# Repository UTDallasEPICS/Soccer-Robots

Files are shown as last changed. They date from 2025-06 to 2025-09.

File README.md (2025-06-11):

# Soccer Robots CS (UTDesign EPICS)

<!-- markdownlint-disable-next-line MD033 -->
<details><summary><h2>Table of Contents</h2></summary>

- [Conceptual Overview](#conceptual-overview)
- [Repository Branches Map](#repository-branches-map)
- [Functional Requirements](#functional-requirements)
- [Third Party Integrations](#third-party-integrations)
- [Tech Stack](#tech-stack)
- [Deployment Notes](#deployment-notes)
- [Migration Scripts](#migration-scripts)
- [Setting Up Development Environment](#setting-up-development-environment)

</details>

## Conceptual Overview

The Jonsson School UTDesign program serves students from UTDesign Capstone, EPICS, Makerspace and Startup. Our partner is Tim Givens, the UTDesign Studio Assistant Manager, who has the following mission:

*To bring UTD to the forefront of robotics competitions while collaborating with local high schools to get more kids engaged in robotics and STEM.*

Soccer Robots is an interactive live-fed soccer game between two robots where players can control their robots remotely over the internet. The Soccer Robots team is split into CS and Engineering teams. We are Soccer Robots CS, tasked with

- Handle serving webpage
- Handle user accounts through Auth0
- Integrate Twitch livestream
- Display game information such as time and scoreboard
- Implement queue system
- Set up and record matches
- Forward wasd inputs from players to Engineering team (Raspberry server)
- Communicate with Engineering team for robots' status

Our project not only caters to the entertainment needs of our users but also serves as a captivating demonstration of UTDesign's capabilities!

## Repository Branches Map
- main: Website / user side of project
- main_robot: Main branch for the robot side of the project
  - esp32_code: Development branch for robot side of the project
- raspberry_pi: Main branch for web/game server code. A raspberry pi is used to host the website, manage the game, and bridge control from user to robots.
  - oled_pi: Contains a service script that runs on raspberry pi startup. This displays IP information of the raspberry pi. 

## Users/Roles

#### Guest

- can watch the game

#### Registered User

- can watch the game
- join/leave/confirm queue
- can play the game (wasd inputs)

#### Admin 

- The Admin shall be able to change match settings
- The Admin shall be able shutdown the Robot

## Functional Requirements

### Website

- The website shall display a game livestream in under 10 second latency
- The website shall display a timer/scoreboard for the current match, showing the usernames of the players as well as their respective scores
- The website shall display the game queue
- The website shall display additional information such as About Us, How to Play, and Help
- The user shall be able to login and logout through Auth0
- The user shall be able to select a new username
- Newly registered users shall be able choose a unique username (2-15 characters, alphanumeric except for dashes ```-``` and underscores ```_```)

### Queue System

- Logged in users shall be able to click on a “Join Queue” button to enter the queue
- Users in the queue shall be able to click on a “Leave Queue” button to leave the queue
- The queue shall not allow duplicate users in the queue
- The queue shall display multiple upcoming matches by placing later matches below earlier matches
- When a match is done and there are at least two players in the queue, the system shall send a confirmation popup to the next two players in the queue with the option to “Accept” or “Decline”
  - In a confirmation popup, the player shall be able to click “Accept” within 10 seconds to agree to join the match
  - When both players of a confirmation popup click “Accept”, both players shall be able to enter a soccer robot match and each control a robot
  - In a confirmation popup, the player shall be able to click “Decline” within 10 seconds to refuse to join the match and leave the queue
  - In a confirmation popup, the system shall kick a player from the queue if the player does not click either “Accept” or “Decline” within 10 seconds

### Admin Panel

- User with an admin privileges can shutdown the robot.
- User with admin privileges can also change the match settings such as match length, num of players in a match.
- The Admin panel will be pn the secondary navbar adn when clicked we will get a popuo
  - The popup has two buttons that says shutdown and match settings
    - When users clicks on shutdown it verifies the user previleges and if admin it sends signal to the raspberry pi.
    - when clicked on match settings we wll get a drop down that asks for number of players and match length. The data is saved in the database when clicked save.

### Leaderboard

- The leaderboard shall show the columns of the players wins, losses, total goals scored, total games played, and win/loss ratio
- The leaderboard should appear in modal
- The leaderboard shall be shortable by the columns representing: goals, wins, losses, win/loss ratio, and games played of each player
- The leaderboard shall show the top 5 players
- The leaderboard data shall update after every game

### Soccer Robot Game and Sending Signals

- The system shall be able to check whether the robots are in a "ready" state (as communicated by the Engineering team)
- A player who is entered into the soccer robot match shall be authorized and able to control one of the soccer robots for the duration of the match using WASD keys
- The system shall be able to receive “goal score” signals and update the current scoreboard accordingly
- Upon game completion, control of the soccer robots shall be revoked from the completed game’s players
- Upon game completion, the system shall reset the scoreboard scores to 0 and timer to its initial value

### Data Storage

- The system shall store, for each user, a unique username and email address
- The system shall store, for each completed match, the two players who played in the match, the final score of each player, and the datetime of the match

## Third Party Integrations

- Auth0 for authentication
- Twitch for live-streaming soccer arena
- Janus WebRTC Plugin for improved live streaming

## Tech Stack

- Nuxt.js
- Node.js
- SQLite and Prisma
- Postman

## Deployment Notes

N/A

## Migration Scripts

N/A

## Setting Up Development Environment

Ensure Node.js, npm, Visual Studio Code, Git, WSL2 (windows only) are installed. Auth0 account is needed.

### Install the repo

```bash
git clone https://github.com/UTDallasEPICS/Soccer-Robot-Web.git
cd Soccer-Robot-Web
npm install
```

### Set up Auth0

In the Auth0 application dashboard, configure the following with the appropriate port. Nuxt default port is 3000. The slashes ```/``` are very important. If using a different host than **localhost**, change **localhost** value accordingly.

- Allowed Callback URLs

```bash
http://localhost:PORT/api/callback
```

- Allowed Logout URLs

```bash
http://localhost:PORT/api/logoutcallback
```

- Allowed Web Origins

```bash
http://localhost:PORT/
```

Get the signing certificate from the Auth0 application and create a root-level cert-dev.pem containing the certificate.
```bash
-----BEGIN CERTIFICATE-----
...
-----END CERTIFICATE-----
```

### Initialize .env variables

#### Option #1

- Copy your mentor's .env file into the root directory

#### Option #2

- Create an .env file in the root directory
- Fill with necessary information based on **.env.example**

#### Some notes

- Some are ports duplicated because I wanted to follow naming convention without NUXT_ prefix. For example, all instances of **PORT2** should be the same port
- **LOCALHOST** can be localhost (for development) or host server's IP address
- **NUXT_AUTH0_CLIENTID**, **NUXT_AUTH0_SECRET**, and **NUXT_ISSUER** depends on Auth0 application
  - The slashes ```/``` are very important.
- **NUXT_CHANNEL_NAME** and **NUXT_PARENT_NAME** depends on Twitch account
- **CONTROLLER_PASSWORD** and **CONTROLLER_ACCESS** are useless because of randomized password rotations :)
- Make sure to put in the proper value for "PI_ADDR". The ip address should be displayed on its screen when the Pi is connected to "RPIHotspot". If the hotspot isn't available, try connecting the monitor to the raspberry pi, and seeing what wifi it's connected to. That should give you details about its current address. Note that you may need to connect your own hotpsot to the raspberry pi, if the RPIHotspot isn't set up yet.

### Set up database

```bash
npx prisma migrate dev --name init
```

### Start all servers

**MAKE SURE THE RASPBERRY SERVER IS RUNNING FIRST**.\
Then, in separate terminals, execute the following commands

**Additionally, make sure the Game Manager server is ran before Controller server, and reminder
that the Raspberry Pi should have 3 processes running, as mentioned in the raspberry pi branch.**

```bash
# this starts Game Manager server
npm run bootgame
```

```bash
# this starts Controller server
npm run bootcontrol
```

```bash
# this starts Nuxt server
npm run dev
```

### Useful dev tips

#### Prisma GUI to view database

```bash
npx prisma studio
```

#### If exposing host IP address is needed, append ```-- --host```

```bash
npm run bootcontrol -- --host
npm run bootgame -- --host
npm run dev -- --host
```

### For development without Soccer Robot Hardware's Rasberry Pi ###
```bash
npm run bootpi -- --host
```

#### Custom package.json scripts

tsx is used to run Typescript files

```json
"scripts": {
    ...
    "bootgame": "tsx server/Game_Manager/src/index.ts",
    "bootcontrol": "tsx server/Controller/src/index.ts",
    ...
}
```

#### Use Postman to test HTTP and WebSockets

#### Mermaid is useful to document flowcharts and sequence diagrams in markdown

- <https://mermaid.js.org/>
- See ./notes

#### Documentation

See ./notes, ./figma

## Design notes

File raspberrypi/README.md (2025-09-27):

# Starting the Raspberry Pi

## Setup

Before starting anything, make sure you have installed the Driver for the WI-FI Adapter. You must also install all libraries to use the camera.

### Installing Camera Libraries

You will need libcamera and picamera2 
**sudo apt install libcamera**
**sudo apt install -y python3-picamera2**
[TROUBLE SHOOTING](https://www.youtube.com/watch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)

### Installing WI-FI Driver
When testing if the driver is installed type lsusb in the command line to find usb name and position. Type lsusb -t and find usb. look for "Driver=". If there is nothing there like rtl8852bu then the driver is not installed.

If this is the case, find the required chipset.
Install the chipset onto the driver by cloning the driver repo best suited and following the steps.

Ensure you have the right developer tools.
**sudo apt install -y build-essential bc dkms git**

### Starting the hotspot
To broadcast the hotspot, run the following command to create a hotspot, replacing the <hotspot name> and <hotspot password> placeholders with a hotspot name and password of your choice

**$ sudo nmcli device wifi hotspot ssid <hotspot name> password <hotspot password> ifname wlan1**

### Accessing the Raspberry Pi

After turning on the Pi and connecting to the internet, use your terminal to SSH into the Pi by typing <username>@<ipaddress>, where "timthegoat" is the current username and the ipaddress is your local Pi address shown below(NOTE: Once hotspot is setup this will default to 10.42.0.1).


NOTE: when attempting to run the servers, you'll need to activate the virtual
environment (which includes things like the libraries used). To activate this,
create a Python (3.11) virtual environment from the requirements.txt file.

Also, make sure when communicating with the server that both **ControllerPi.py** and **GmServerPi.py** are active. Even if you're just testing the GM server, it will appear to not work unless
the controller server is also active.
(Note: Current Python Version 3.11.2)
### Startup
run start_soccer_robot.sh
**bash start_soccer_robot.sh**

If you run the script, you do not have to do the following: 

To run this, you want to first activate **EspManager.py**. This is basically the process that will communicate with the Raspberry Pi's. It does this by creating child processes, and each child
makes a TCP connection with a single ESP, and communicates with the parent back and forth with unnamed pipes. **ControllerPi.py** and **GmServerPi.py** will send relevant information to **EspManager.py**
through another socket connection. Here's a diagram to explain the purpose of each process a bit better (apologies for the poor quality).
better diagram

Now to run the Raspberry Pi server, we will first run **EspManager.py**, move that to background, then run **GmServerPi.py**, move that to background, then run **ControllerPi.py**, move that to background,
and that will be all you need to do. Note that you **MUST** run it in this order, otherwise because of the order of socket connections it won't work properly.
RECAP:
1. python EspManager.py (next CTRL+Z to pause, then type "bg" to place process in background)
2. python GmServerPi.py (next CTRL+Z to pause, then type "bg" to place process in background)
3. python ControllerPi.py
(You can use "ps" linux command to check the proccesses that are running, it will have a process id.
If one of the python programs have an error, then use the linux command "kill -9 [process-#]")

Next, on the website do the npm run bootgame, npm run bootcontrol (run this after bootgame always) npm run dev and stuff. Now,
get two people to start the game, and profit as you see the robot moving, the updated timer, and the updating score.
RECAP:
1. npm run bootgame
2. npm run bootcontrol
3. npm run dev

As for the camera, you will be able to stream it by running **"cleanCode.py"**, which will begin streaming the camera to http:IP-ADDR-PORT, as long as it's connected to wifi and the camera itself is
connected onto the Raspberry Pi. Note that while we're temporarily using the smaller camera, we want to use the Arducam camera eventually because it has a wider lens and thus can capture the game better.
Research may need to be done on how to implement it with the Arducam, as there were some difficulties doing so.

So overall, all the scripts you'll really need to run the website will be in the "scripts" directory, and you just need the following 5 files: **EspManager.py, ControllerPi.py, GmServerPi.py, ESPClient.py, and cleanCode.py**. ESPClient.py is used to easily handle connections between the ESP and the Pi.

Additionally, we did have code for the camera to detect charging stations, and give commands to the esp32 so that the robot will move towards the charging stations. The code for this may be in "apriltagLiveFeed.py",
ask your mentor for further details.

# File Descriptions

## Startup

### EspManager.py

This takes in data about motor inputs for each robot and signals from the game manager (game start, robot ready check, game end), and sends the appropriate data to each robot.

To connect with each robot, it forks itself (basically like makes a clone of the program that also starts at the same code line where the fork was) based on however many robots there are. If there are 2 robots, for instnace, there will be 2 forks, and thus 2 child processes will be made.

May need to research pipes, forking, piping, and processes to understand this.

Then, when it receives a request for ready connection from GmServerPi.py, it relays that through pipes to its child processes, which then send a message to the robots asking if they're ready. If they are, they should return back their own success message successfully. Then if all robots returned success message, send that to the game manager file which then tells that to the website.

Also, for motor inputs, ControllerPi.py sends its ID alongside the motor inputs. EspManager checks the ID and sends it to the correct child process, which then sends those inputs to the esp32.

It also has shared memory shared with GmServerPi.py, which is where the current game timer is stored. Basically, when the game ends, it puts in the shared memory that the game is over. EspManager reads from this frequently, and when it sees the game is over, it can shut off communication with the robots, and prepare for reconnection.

### ControllerPi.py

This connects with the website's Controller file, and when the website sends inpts from the user, it directs those inputs to EspManager.py. Pretty straighforward, though it also checks if the input the user sends is the same input as before. If it is, then it doesn't send it, as that doesn't change anything.

### GmServerPi.py

This connects with the website's game manager file. It handles and responds to certain messages from the website. For example, if it receives a packet to check if robots are ready, it sends that request to espmanager, gets a response, and sends that response back up to the website.

When it receives game start command, it begeins running the game, waiting until the timer's up, and when it is it puts in shared memeory with GmServer that time is up, to let it know to disconnect the robots. Then it restarts with waiting fora game to start. It also sends the timer to the website, as it actually is what has the decreasing timer.

### ESPClient.py

This is just a class where each object represents a connection with an esp32, used as a helper function. It has functions like trying to connect to the esp, sending data, and receiging data, alongside error handling too.

# Camera

## cleanCode.py

This creates a page that's hosted on the raspberry pi at a ip address and port to stream the camera display to. It initializes with the camera and starts a server to host the stream on, and connects them to the stream.... somehow. Probably when it calls self.wfile.write(frame), where it writes the current frame of the camera.

## combinedCam.py

This is like the file above, but this time it makes it so if there's keyboard presses of WASD on the raspberry pi, it moves the camera lens to show a differnet place of the field. At least, I'm assuming that's the intention.

NOTE: THIS ONE MAY BE OUTDATED; CHECK WITH DAMIAN ON THIS.

## apriltagLiveFeed.py

This is basically exactly like the above, but now if you put an april tag in front of the camera, this code will detect that april tag. The code to detect the april tag will be useful likely, use this as reference when implementing the algorithm to send robots to charging stations. It may be outdated in the same way that combinedCam is outdated.

## backtracking.py

There isn't any file named  this, I assume it's just backTest.py. This seems to first do the same as above, streaming it but also showing the april tag on the screen. Right now, it puts the movement instruction on the frame, so ideally the only thing that needs to be done is sending it. 

It seems right now it's configured to send 2 pieces of data to the motor: first, the direction of movement (rotationg left, rotating right, moving backwards, moving forwards, stopping) as well has how much to rotate in each direciton. Now, main issue will be configuring that to become packets to send to the esp32. Have fun with that! 

Also note that each car has 4 states. State 0 is rotating to face target, state 1 is moring towards target, state 2 is doing final rotation, and state 3 means finished arriving and rotating at charigng station.

## backupTag.py

This seems to be like a prototype of the one above? It uses a file that doesn't exist anymore (backtracking.py, though an archive of it is at https://github.com/UTDallasEPICS/Soccer-Robots/blob/1eee7dc0c4098b2c6e86b0c17d89b73867ff42a8/raspberrypi/scripts/archive/Backtracking.py.txt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). Even so, backupTag.py references a method in backtracking.py "get_direction", that I can't find in the backtracking.py archive file.

## carConnect.py

This is a file that was used to connect to the ESP32. Back when I made the ESPClient.py file I didn't know this one existed, but all it does for now is just connect and send a handshake, and that's it. Now though, it seems we don't need it since ESPClient.py and ESPManager.py does everything this would've already done.

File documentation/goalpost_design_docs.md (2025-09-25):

Main objective was to come up with goalpost design, so I created 2.

### goalpost.SLDPRT
- Simplified design of Su25, made bigger about 15in wide to accommodate ball and bigger robots.
- Box style design, ball exits on the side
- Main concern: ramp may not be steep enough to let ball roll to the side
- NEEDS TESTING for the above design to ensure ball does roll
- Maybe get a better ball or treat ramp surface??
### goalpost_alt.SLDPRT
- Very similar to previous, however ball exits from the back
- Ramps are steeper to shouldn't have an issue with ball rolling
- Main concern: ball exits through the center back, how do we reliably get it to the launch mechanism and go out the front???
### 3D Printing
- Need to 3D print one of these, Bambu Studio has tools to break this into parts but need to familiarize myself
- Also need a 3D printer, EPICS lab one is kind of small so try to get access to something else to speed things up
### launcher_assembly.SLDASM
- Uses a "flywheel" to launch the ball, much like tennis ball launchers
- The "wheel" in this model is a LEGO 56x26 tire, part number 55976

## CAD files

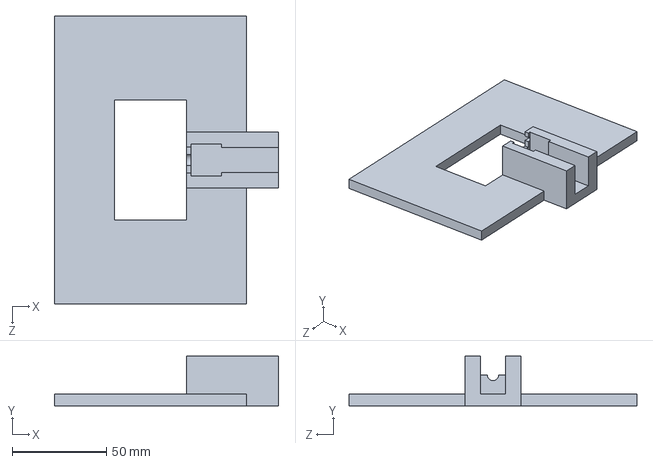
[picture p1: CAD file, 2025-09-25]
cad/F25/motor_holder.SLDPRT
118.7 x 26.4 x 152.4 mm

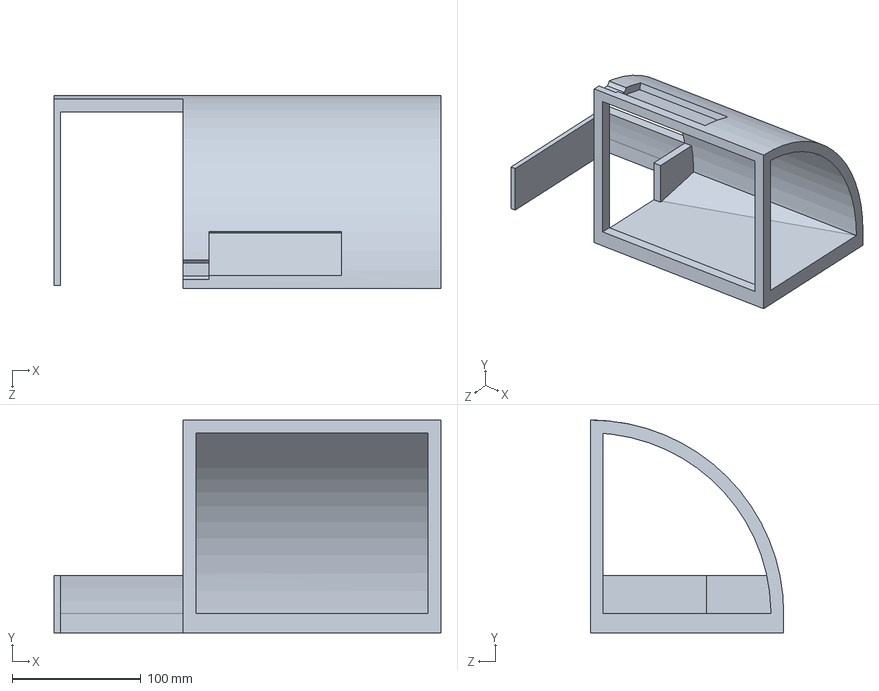
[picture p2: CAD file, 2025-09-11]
cad/Su25/GOALPOSTFINAL.SLDPRT
300.0 x 165.0 x 150.0 mm

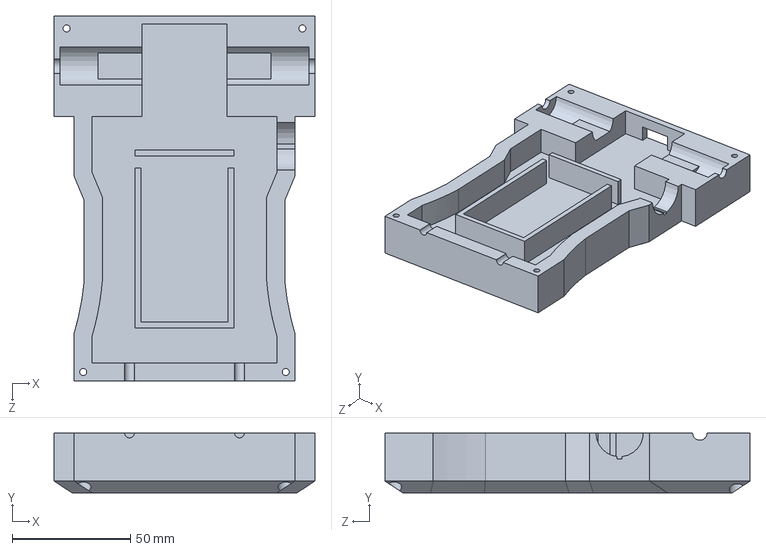
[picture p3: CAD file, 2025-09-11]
cad/Su25/chassisfinalbottom.SLDPRT
110.1 x 25.3 x 154.1 mm

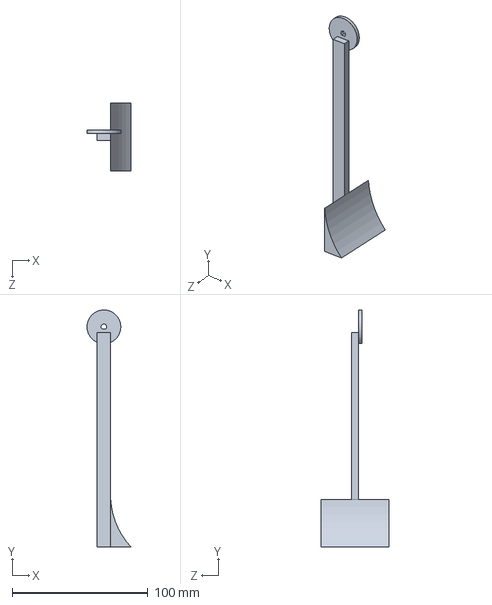
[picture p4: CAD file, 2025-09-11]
cad/Su25/GOALPOSTHANDLE.SLDPRT
32.5 x 174.6 x 50.0 mm

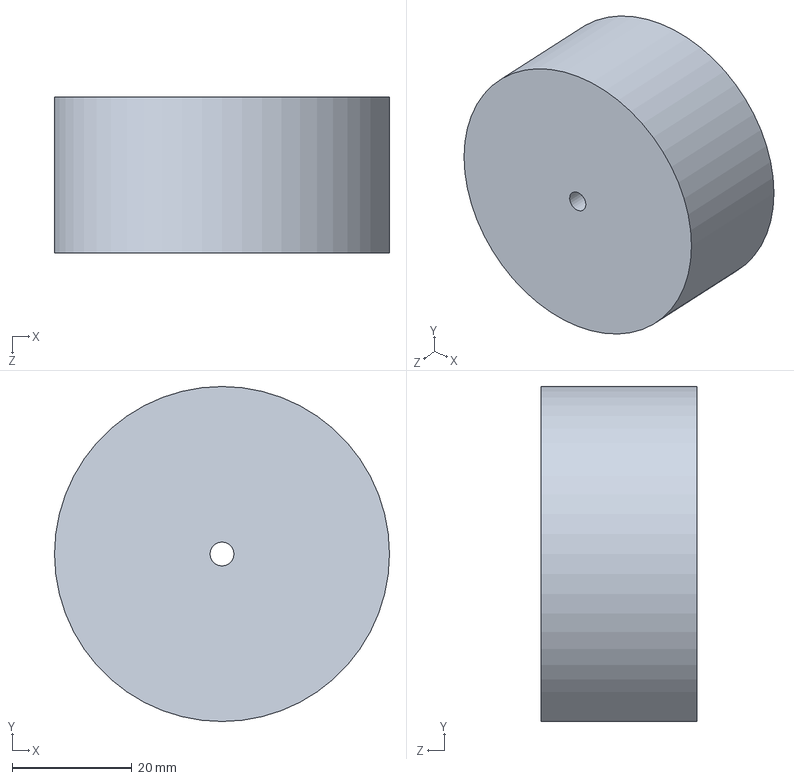
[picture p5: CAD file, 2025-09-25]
cad/F25/launcher_wheel.SLDPRT
56.0 x 56.0 x 26.0 mm

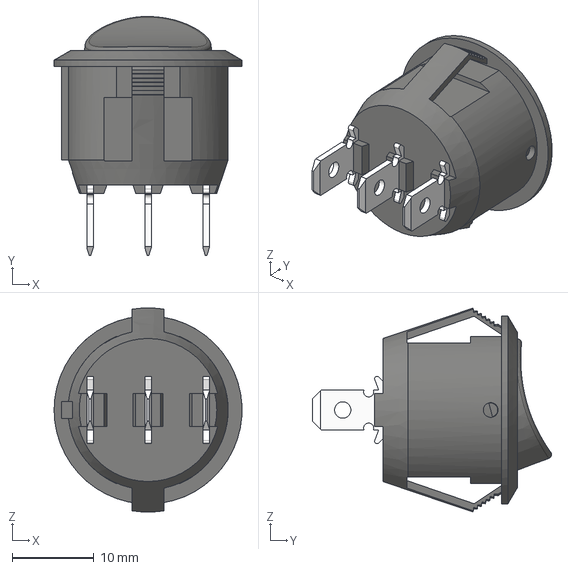
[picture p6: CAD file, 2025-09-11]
cad/Su25/SWITCH.stp
23.0 x 29.2 x 25.0 mm

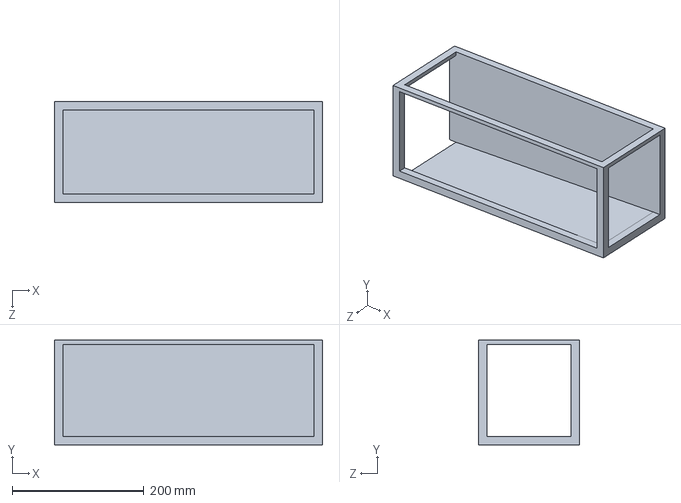
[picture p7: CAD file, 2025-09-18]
cad/F25/goalpost.SLDPRT
406.4 x 158.8 x 152.4 mm

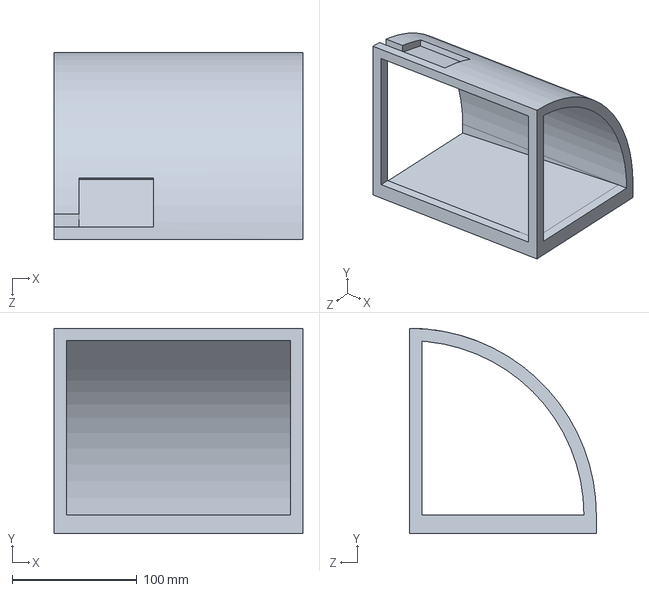
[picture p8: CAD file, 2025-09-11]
cad/Su25/goalpost.SLDPRT
200.0 x 165.0 x 150.0 mm

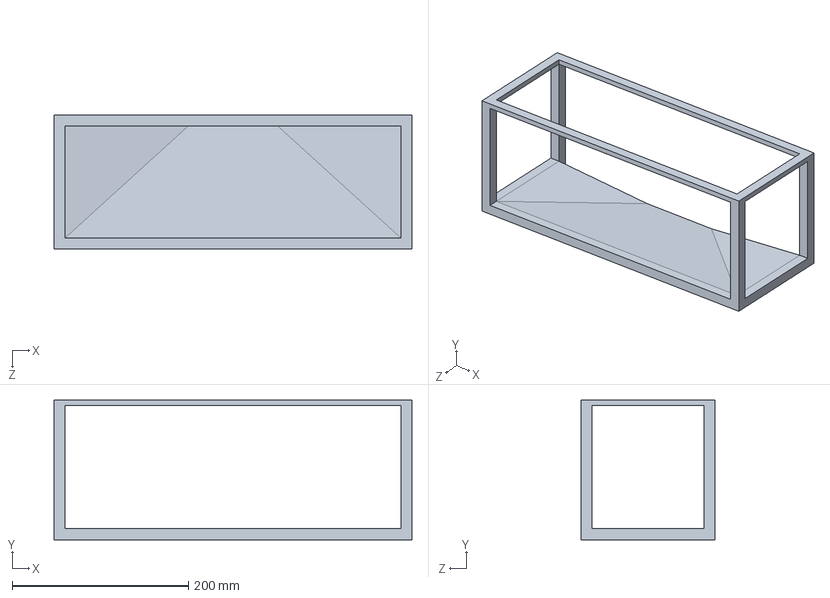
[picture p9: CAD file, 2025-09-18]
cad/F25/goalpost_alt.SLDPRT
406.4 x 158.8 x 152.4 mm

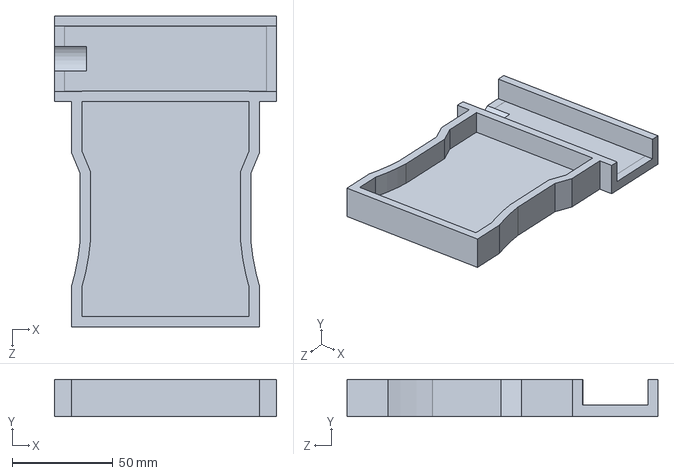
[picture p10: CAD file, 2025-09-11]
cad/Su25/newchassis5.SLDPRT
110.1 x 18.4 x 154.1 mm

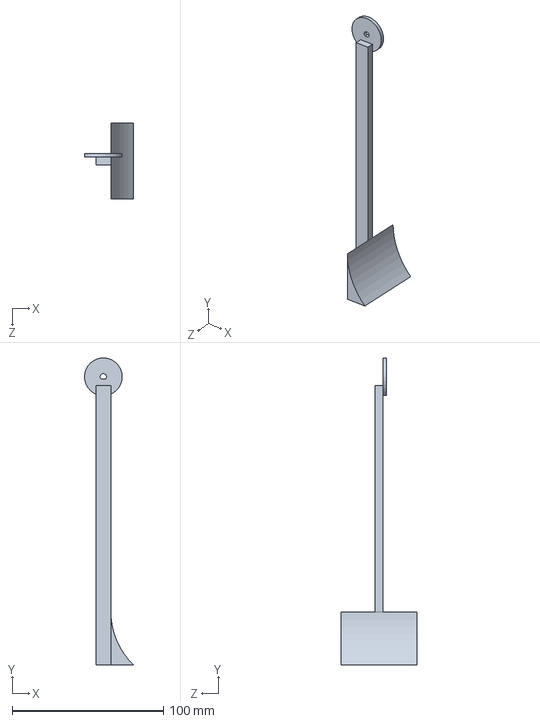
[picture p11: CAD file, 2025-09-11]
cad/Su25/HANDLEFINAL.SLDPRT
32.5 x 203.2 x 50.0 mm

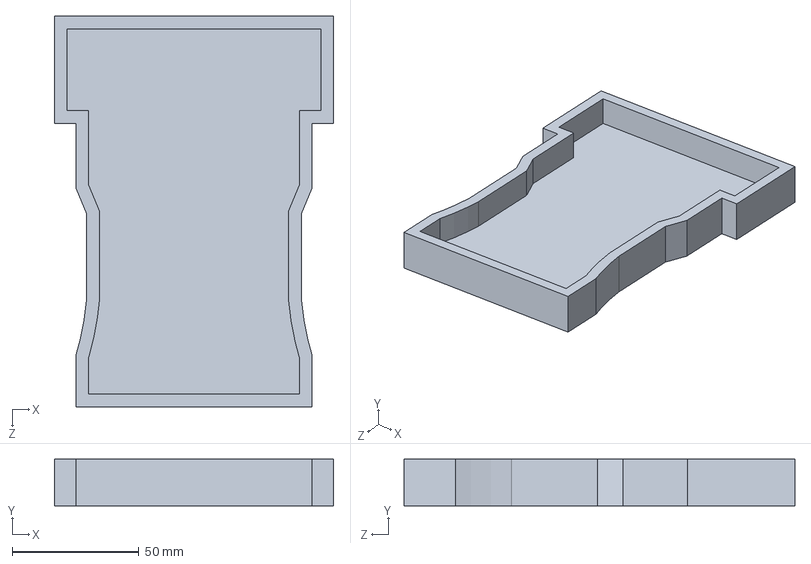
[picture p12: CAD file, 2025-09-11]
cad/Su25/newchassis.SLDPRT
110.1 x 18.4 x 154.1 mm

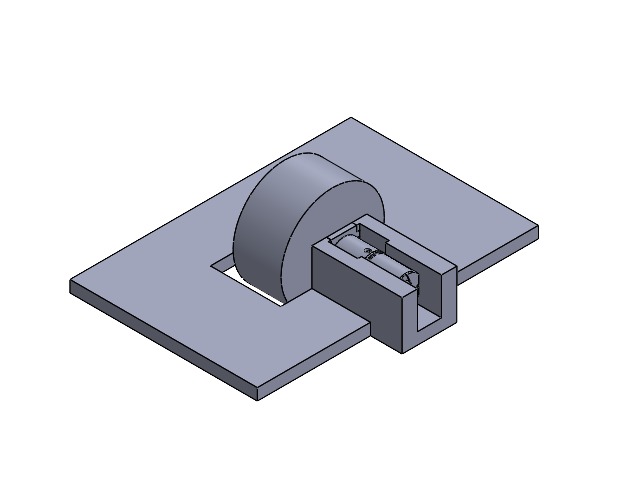
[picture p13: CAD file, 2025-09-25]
cad/F25/launcher_assembly.SLDASM
motor_holder
45T______15_M0.3X45_GMP16T-030PA-22.6 4.0mm_MOTOR(2)_GMP16T-030PA-22.6 4.0mm_MOTOR.STEP
030DIANJI-1_GMP16T-030PA-22.6 4.0mm_MOTOR(2)_GMP16T-030PA-22.6 4.0mm_MOTOR.STEP
4.7_______GMP16T-030PA-22.6 4.0mm_MOTOR(2)_GMP16T-030PA-22.6 4.0mm_MOTOR.STEP
_________GMP16T-030PA-22.6 4.0mm_MOTOR(2)_GMP16T-030PA-22.6 4.0mm_MOTOR.STEP
_______GMP16T-030PA-22.6 4.0mm_MOTOR(2)_GMP16T-030PA-22.6 4.0mm_MOTOR.STEP
22__________8.6_GMP16T-030PA-22.6 4.0mm_MOTOR(2)_GMP16T-030PA-22.6 4.0mm_MOTOR.STEP
______(____)_GMP16T-030PA-22.6 4.0mm_MOTOR(2)_GMP16T-030PA-22.6 4.0mm_MOTOR.STEP
motor_retainer^launcher_assembly
launcher_wheel

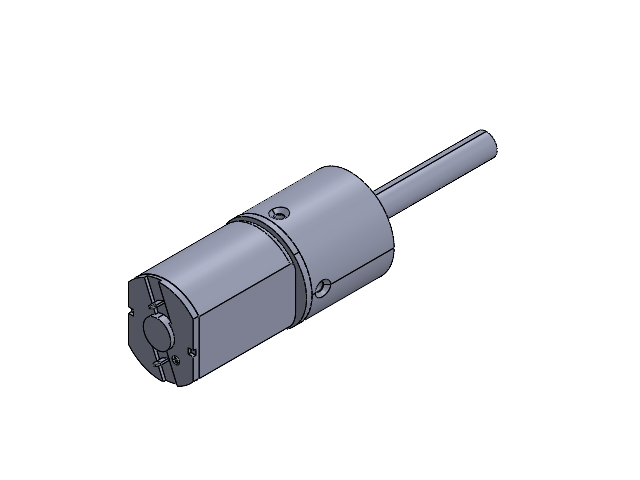
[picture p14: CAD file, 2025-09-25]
cad/F25/motor.SLDASM
45T______15_M0.3X45_GMP16T-030PA-22.6 4.0mm_MOTOR(2)_GMP16T-030PA-22.6 4.0mm_MOTOR.STEP
030DIANJI-1_GMP16T-030PA-22.6 4.0mm_MOTOR(2)_GMP16T-030PA-22.6 4.0mm_MOTOR.STEP
4.7_______GMP16T-030PA-22.6 4.0mm_MOTOR(2)_GMP16T-030PA-22.6 4.0mm_MOTOR.STEP
_________GMP16T-030PA-22.6 4.0mm_MOTOR(2)_GMP16T-030PA-22.6 4.0mm_MOTOR.STEP
_______GMP16T-030PA-22.6 4.0mm_MOTOR(2)_GMP16T-030PA-22.6 4.0mm_MOTOR.STEP
22__________8.6_GMP16T-030PA-22.6 4.0mm_MOTOR(2)_GMP16T-030PA-22.6 4.0mm_MOTOR.STEP
______(____)_GMP16T-030PA-22.6 4.0mm_MOTOR(2)_GMP16T-030PA-22.6 4.0mm_MOTOR.STEP

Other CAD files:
cad/Su25/GOALPOSTASSEMBLY.SLDASM
cad/Su25/ROBOTASSEMBLY.SLDASM
cad/Su25/HANDLE.SLDPRT
cad/Su25/goalpost2.SLDPRT
cad/Su25/BUMPERFINAL.SLDPRT
cad/Su25/CHASSIS.SLDPRT
cad/Su25/ESP32 Robot Wheel v7.f3d
cad/Su25/HANDLEFINAL.STL
cad/Su25/MOTOR.SLDPRT
cad/Su25/Part3.SLDPRT
cad/Su25/Raspberry Pi 4 Case (Soccer Robots) v18.f3d
cad/Su25/Robot Assembly.SLDASM
cad/Su25/Soccer Robot Chassis v9.f3d
cad/Su25/chassisfinal.SLDPRT
cad/Su25/chassisfinal.STL
cad/Su25/chassisfinalbottom.STL

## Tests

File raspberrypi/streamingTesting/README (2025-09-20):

Make sure you have Janus, Gstreamer, and dependencies installed.
When installing Janus, enable websockets.
The .jcfg files are new config files for Janus implementation. They can be found at /opt/janus/etc/janus once you have Janus installed.
There are still some problems with the test website (index.html) but its able to be viewed through the Janus streaming demo.

To test GStreamer: "gst-launch-1.0 libcamerasrc ! video/x-raw,colorimetry=bt709,format=NV12,width=1280,height=720,framerate=30/1 ! queue ! jpegenc ! multipartmux ! tcpserversink host=127.0.0.1 port=5000"
To run Janus: "/opt/janus/bin/janus"
To test webpages: "python -m http.server 8080"

I would recommend opening new terminals for each to see the logs.

Link to my google docs for my messy notes and work: https://docs.google.com/document/d/1VDXmJoVrWC7JGhiUmJSp1YNq2BlKNLPrcJ04FbnOHGs/edit?usp=sharing

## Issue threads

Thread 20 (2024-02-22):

[Feature] Website Basic Homepage Layout and Basic Functionality (Scoreboard/Timer, Video Player Design)

CrazEpic, 2024-02-22:
**Feature Description**
Implement the basic look and functionality of the website homepage. Design and functionality choices are closely based on Jahnzeb's Figma. This feature is mainly for defining the homepage layout.

**Requirements**
- Scoreboard design: Display both player's scores and usernames.
- Timer design: Display timer in MM:SS.
- Video player design: An empty container with an HTML video tag is sufficient for now.

**Additional context**
- Refer to Jahnzeb's Figma for UI design and functionality
- Frontend design and functionality will still be incomplete. It will be progressed as backend functionalities are added.
- No backend functionality has to be implemented in this issue, but make sure frontend functionality makes sense. For example, implement buttons where the Figma has buttons and text fields where the Figma has text fields. This is especially important for CSS grids for the queue system.

Closed 2024-03-24.

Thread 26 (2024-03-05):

[Feature] Style Homepage Top Nav Bar (Sign-In, Log-In) and Include UTD Logo

jahnzeb-bastaki, 2024-03-05:
Want the appropriate styling of the top nav bar (UTD Logo, Sign Up, Log-In) from the figma model

Requirements:
• Add Margin/Padding to Sign-Up Button
• Add Margin/Padding to Log-In Button
• Add UTD Logo to page

Optional Requirement:
• If possible, create a component called Top Nav Bar that holds the UTD Logo, Sign-Up, and Log-In Button

Closed 2024-03-27.

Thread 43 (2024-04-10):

[Feature] SIngular SignUp/LogIn Button

jahnzeb-bastaki, 2024-04-10:
**Feature Description**
A UI change where we instead of having two buttons for a Log In button and a Sign Up Button, rather we just want one button since if the user isn't registered, Auth0 will take care of that.

**Requirements**
Replace the two buttons with one button, while still keeping the integrity of the UI components.

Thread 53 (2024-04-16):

[Feature] Game Manager Server: Simulate Game Cycles

CrazEpic, 2024-04-16:
**Feature Description**
Simulate game stages: NOT_PLAYING, SEND_CONFIRM, PLAYING, RESETTING.

**Requirements**
- During NOT_PLAYING, the server will check queue if sufficient players are available. If yes, a confirmation request will be sent to the next 2 users in queue
- During SEND_CONFIRM, the server will handle received confirmations and progress to PLAYING if 2 accepts are received.
- During PLAYING, if the timer reaches 0, the server will stop the game and progress to RESETTING.
- During RESETTING, the server will remove the previous players from the allowed players list in the Controller server.

Closed 2024-04-23.

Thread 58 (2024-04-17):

Change from PUG template to standard HTML templage [BUG]

jahnzeb-bastaki, 2024-04-17:
**Describe the bug**
Some of the component files have the pug templates instead of standard HTML templates, so we need to change that.
The components that have the pug file are:
- AboutUsOverlay.vue
- Button.vue
- HelpOverlay.vue
- HowToPlayOverlay.vue

**To Reproduce**
Just go to the template

**Expected behavior**
The previous component files should have standard HTML templates

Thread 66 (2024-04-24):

[Feature] Switch to tsx for running index.ts files

CrazEpic, 2024-04-24:
**Feature Description**
Switch ts-node for tsx to fix esm and commonjs issues

Closed 2024-04-24.

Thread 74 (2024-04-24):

[Feature] End of Semester Requirements (Spring 2024)

CrazEpic, 2024-04-24:
# End of Semester Requirements

The following checklists are what is required for your code to be considered acceptable at the end of the semester. The general purpose is to ensure that someone can run your code without encountering any errors and everything the next team needs will be easy to find. ***If your project cannot be run based on the information and files on GitHub, your final project grade will be greatly reduced and/or your team will receive an incomplete until the information needed to run your project is provided!***

One potential way to make it easy to track all of these tasks is to create issues for each of the required tasks ([see this page about GitHub issues](https://docs.github.com/en/issues/tracking-your-work-with-issues/quickstart#adding-a-task-list)). The first item in the [Project Structure/Files](#project-structurefiles) section would look something like this to automatically check the box when issue 3 is closed:

```markdown
- [ ] #3 Database Files
```

## Project Structure/Files

These requirements must be met (in the main branch of your project) by the time your final report is due.

- [x] The most up to date version of all frontend and backend code
- [x] Database Files
  - [x] If using docker: `docker-compose.yml` at top level for project database.
  - [x] Database Schema
    - If using Prisma: `schema.prisma` in a top level `prisma` folder
    - If using other database: A file with a descriptive name used to create your database schema (e.g. `schema.sql`)
- [x] `.env.example` file containing NON-SENSITIVE environment variables (Auth0 Issuer, dev database url, etc). Sensitive environment variables should be replaced with example data such as `CLIENT_SECRET='EXAMPLE_CLIENT_SECRET'` so that future groups know that the environment variable is required.
- [x] Figma design files in a top level folder named `figma`.
- [x] Any migration scripts, dev scripts, etc. (if any exist) belong in a top level `scripts` folder. If the project has separate frontend/backend folders, the `scripts` folder should be in the backend folder.
- [x] Any other important files should be included in an appropriately named folder (such as `docs`, `documentation`, `notes`, etc.).

## Documentation

A README.md file at the top level containing the following:

- [x] Conceptual overview - what is the project intended to accomplish?
  - Include a broad description of the different types of users/roles and what they do.
- [x] Functional requirements (broken down by page) - what are the discrete operations the app needs to be capable of?
- [x] Third party integrations and what they do in this project - HubSpot, Stripe, Auth0, etc.
- [x] Tech Stack
  - Include frontend framework (React, Vue, Svelte, etc.)
  - Include backend framework (Express.js, etc.)
  - If you use a meta framework, where the frontend and backend are combined, then you do not need to differentiate between frontend and backend (Next, Nuxt, Sveltekit, etc.)
  - Database (PostgreSQL, MySQL, MongoDB, etc.)
  - Other important packages (UI plugins, database connectors like prisma)
  - Other tools used/needed (such as Postman)
- [x] Deployment notes (if project is currently or in the process of being deployed) - is the partner running the application on their own servers or are they using something like AWS or Azure?
- [x] Migration scripts - do we need to import any data from an existing system that the partner is using?
- [x] ***Instructions for setting up the development environment!!!*** Assume that the needed software is already installed (Node.js, Docker, etc.).
  - How do you start your project?
  - How do you initialize the database?
  - How do you set up authentication?
  - Etc.

These should be high level - you should not be explaining every line of code.

CrazEpic, 2024-04-24:
No GitHub wiki 😃

CrazEpic, 2024-05-08:
We're done. Frieren sleeping is like me. 💤
```
,,,,........,,.............*,///**,,**////////////////////.#......,,,./((.,,,.,,..,.....................................
,........,.............. **./////**,.**/////////////////*...(,..,,,,.(((((.((##(((( .......................... .........
.................. .,**.,,,*///////**,,//////////////////.,.*(.,,,.*((((((..,.,.,...,...................................
............... */.....**,,/////////***,,/////////////////.,.(..,((((((/.,,,,,...,,.......................... ..........
...............**/**,.***.////////////****,//////////////.*.*/*(((((((.,,,...,,,............................. ..........
.............../**/*.***,*////////////*.****,,////////*,**, /,*/////(.,.,,,,..,............................. ...........
.......... .**,.*/******.///////////////,**,***, .,*//////.**,*////**.,.,.,.,..**/,..,,..................... ...........
.......*///./////******,*////////////////,**,.*/////////////*,,.......  ....*/***.,.,.... .................... .........
.....*///.*////*,//****///////////////////.,/*/*//*/*.*((((/((((/,,,*//*,.,(((( .,,.....,........................ ......
.....,/*.//*/*/,///*,**///////////////////.*//*/,,((.,/((((((,*((((/*,* ,/*///***//, ,.............................. ...
......*.*////*.////***/////////////////..,/ */ (,,.((((,((/.(((((///*********// ////**.................................
.. ,**,*/*.*/**////,*/*,....,*.**//////.///,.,./ /((((*((,/(((,.  .*///////////,/**/**** ...............................
//***.,*/*/*..*/*.*/*/////////,*////////.//.**/.(((((,.(.(//***////////////////**/,./.**/.......  ,/*, .................
//*////**,.*.,* .*////////////*,////,*/..,,//,./((/,((/ ////////////////////////,/**/.**** ...........//* ..............
/*/*//***//*,.,**//,/////////////,/(((((.*/*.//,( /(((///////////////////////..,/,///.***/,............./** ............
/,,,**.////*,,,*,*///,////////,/(((((((/*//***,* .((//////.**,,.,*////////////. */**,*//*/* .............**, ...........
***/.*////.*/******///.////*/(((((((((((***///**.,(////////.********,*/////////////.*//**/,. ............,/ *...........
.,.,////,*/////*****/////./(/(((((((((#(((,*/,.**,(//////////*.,*****.*/////***//,*****/**.,**............*,/ ..........
/./////,///////////*//..(////((((((*.,*/(((./..//.///////////////..****.///*//,,/*.***/****,**/*......... **,...........
.*////./////*,,////.,**,(//,,/(((((((((((((*..,**/,**//////////////*.* //.,*//*.,.*/*****.*.**,*/*////***/*.............
/////,////////////*,,*.(((////((((((((#/.*/ .*////*,/////////////////*//////////,*,./*//.**.**,.........................
**,*.,*,.,*,,,,*//.,*,.#((/////((((,,/*,*///.**//*,/*/////////////////////////*,,*,//**.**,****/,.......................
/////..,,,*,,*,,/*,,,.((*((////,,//*,//*///*,*..*///////////////////////////** ,/***/*/,**,//**/*/**.................../
////////.(*. .//.*,,**//*((/////./,*////////*///////////////*///////////////**.,*//.././,*******,**./*****/*,...... *///
//////,*//////,,*,**.(//*(((/////*,/,*//*//*/.//*/////////*/.***/*////*****,**//,*/////,/,*/**/*.../*,.*****/*/*/ //////
/////,/////*.,,*,**.(///*(/..*/////*,/./*//*//*//***///////,/***/*****///.**.*.*//.**//**/****/** ...,/*...... *//(#((#(
////,///*.,*,*,,*,.(////////./,*/////,/,*/////,*.,*//////////,,**/*/***//*  /***.*.,*/**////,/**** ....,/*..,((########(
///*,*.***,*,,**,  ,*//(((*.. */.*////*,*,/***.//*/*,*/.*//////////..*//*.../**/**/*/*/,./*//,**/*/......**(#((######((#
///////****,**,((,...,/((((//////*,///** .***./*/*///////*//**/*//*.,/ , .,/*,*///././/*/***///*****/ ,.(###############
//////*******./((((((((////////////.,,,*//  **..*/,/////////*//*,*/,*/*///*,***,****./.*//*****/*/*/.(#((###############
//////***,***.,../(/////////////////,*,/.,, , ....////*.,***/,,/*,///////, ,.*//*.**/*.*,******/*,/((##((###############
////*,*****.//*,..,.*////////////////*.////*,.///**//,.* .. ,/,*//*/*.//,////.**/*/,,*//**/*.*,/#((#####################
(,*, ...,,,.   .,,*///////////*///////***///,./////***//,////////.*/*//.///// ****.**,***** *(##########################
(((.//((((((((((/,,*/////.,,..,/////////*.//.*,/*/.*///.///////*.//*/**//////,**/**,**/.,,##(#(##########((((########(((
//((#**(((((((((///,/////,/////**/////////./*.*//./////*////*,////////./////,*****/.*/,(#(###############((############(
////(((*,//////**,,.,,,,*///////,*////////*.*///*/////////*,///////,,///*//*******/,/##((################((############(
////////(..*/////////////,*//*///,*/////////.////////////,////**,*////////*,*****,((#(###############((########(#(((((((
*,////////,*////*//////.,/*,/,//*/.*///////*/,/*///////*,//,.*/////////*//.*/*.((##################((((((((((((((((((((#
//**,/*////*/.////*./////,/*. /*./*,*//////*//*,*/////* *///*///////////*., /##(###############(#(((((((((((((((#((((((#
//////,**////// */////*,//////**.,. ,//////*/*/,.*,./ ,*//*//////////*/.,,(##((((################(((((((((((((((((((((((
///////*/.*/*///*,,,,//*///////.*,,,.*////*..**,*,,,,,,.**,,**,,**,,.* ((##((####################(((#(((#(((#(((#(((#(((
///////////*,/////** *//*,... *,,,*,... ,,,,,,,.,,,,,, ,,,,,,,.,,,*./(###(#####################(#(((((((((((((((((((((((
//////////////.///*//* ./*//.,,,,,,,,,,,,,,,,,,,,,,,,,,,,,,,,,.,,*(#((((##################((((((#(((((((((((((((#(((((((
```

Closed 2024-05-08.

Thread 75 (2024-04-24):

[Feature] Game Manager + Controller Integration to Raspberry

CrazEpic, 2024-04-24:
**Feature Description**
Work out the details of endpoints between Game Manager + Controller servers and Raspberry (Engineering) server. Need to communicate with engineering team on this. The idea is upon 2 or more users in queue, Game Manager will ask if Raspberry is ready (this handles charging because engineering should check charging themselves) and start a game if so. The timer and scores are sent from Raspberry to Game Manager. When two players accept and are in game, they will be able to send key inputs to the Controller server, which will forward the inputs to the Raspberry server.

**Requirements**
- When 2 or more users are in queue and the game state is NOT_PLAYING, Game Manager will ask if Raspberry is ready. If yes, Game Manager will start the game state for SEND_CONFIRM.
- Upon a match start, Game Manager will send Raspberry the timer to start with (in seconds). After, the Raspberry server will broadcast to Game Manager the remaining time (in seconds) and the current scores.
- The Controller shall forward KEY_INPUT to the Raspberry server. The format of the payload will be discussed during communication with engineering.
- When the match ends, the Raspberry will send the Game Manager an event "GAME_ENDED" with the final timer (which should be 0) and player scores.

CrazEpic, 2024-04-24:
# SOCCER ROBOTS CS SENT SIGNALS
```ts
{
    "type": "CHECK_READY",
    "payload": ""
}

{
    "type": "GAME_START",
    "payload": {"timer": 300}
}

{
    "type": "KEY_INPUT",
    "payload": {"playernumber": 0 or 1, "keys": "1010"} // wasd
}
```

# SOCCER ROBOTS ENGINEERING SENT SIGNALS
```ts
{
    "type": "IS_READY",
    "payload": true or false
}

{
    "type": "TIMER_UPDATE",
    "payload": 300
}

{
    "type": "SCORE_UPDATE",
    "payload": {"score1": 0, "score2": 0}
}

{
    "type": "GAME_END",
    "payload": {"timer": 0, "score1": 0, "score2": 0}
}
```

Closed 2024-04-25.

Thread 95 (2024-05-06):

[BUG] Confirmation Screen Reset

CrazEpic, 2024-05-06:
**Describe the bug**
Confirmation screen does not reset when a player declines or did not respond.

**To Reproduce**
Steps to reproduce the behavior:
1. Have two players join queue
2. Get the confirmation screen to show up
3. Have at least one player decline/do not respond
4. Wait until timer is over

**Expected behavior**
Every confirmation screen should close after the timer is up.

CrazEpic, 2024-05-06:
I accidentally pushed to main, but it is fixed now from commit 8e0c36f "sent MATCH_CONFIRMATION_RESET when confirmation is up"

Closed 2024-05-06.

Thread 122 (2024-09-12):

[Feature] Need Score and Win increment

AlanMascorro, 2024-09-12:
A sensor will be used to check if a ball crosses the goal.
We need the score to increment according to the goal.
We also need to increment win counter and reset score when enough score has been reached.
Add figma model

Closed 2024-12-06.

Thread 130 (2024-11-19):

End of Semester Checklist

OfekShaltiel-UTD, 2024-11-19:
# End of Semester Requirements

The following checklists are what is required for your code to be considered acceptable at the end of the semester. The general purpose is to ensure that someone can run your code without encountering any errors and everything the next team needs will be easy to find. ***If your project cannot be run based on the information and files on GitHub, your final project grade will be greatly reduced and/or your team will receive an incomplete until the information needed to run your project is provided!***

One potential way to make it easy to track all of these tasks is to create issues for each of the required tasks ([see this page about GitHub issues](https://docs.github.com/en/issues/tracking-your-work-with-issues/quickstart#adding-a-task-list)). The first item in the [Project Structure/Files](#project-structurefiles) section would look something like this to automatically check the box when issue 3 is closed:

```markdown
- [ ] #3 Database Files
```

## Project Structure/Files

These requirements must be met (in the main branch of your project) by the time your final report is due.

- [x] The most up to date version of all frontend and backend code
- [x] Database Files
  - [x] If using docker: `docker-compose.yml` at top level for project database.
  - [x] Database Schema
    - If using Prisma: `schema.prisma` in a top level `prisma` folder
    - If using other database: A file with a descriptive name used to create your database schema (e.g. `schema.sql`)
- [x] `.env.example` file containing NON-SENSITIVE environment variables (Auth0 Issuer, dev database url, etc). Sensitive environment variables should be replaced with example data such as `CLIENT_SECRET='EXAMPLE_CLIENT_SECRET'` so that future groups know that the environment variable is required.
- [x] Figma design files in a top level folder named `figma`.
- [x] Any migration scripts, dev scripts, etc. (if any exist) belong in a top level `scripts` folder. If the project has separate frontend/backend folders, the `scripts` folder should be in the backend folder.
- [x] Any other important files should be included in an appropriately named folder (such as `docs`, `documentation`, `notes`, etc.).

## Documentation

A README.md file at the top level containing the following:

- [X] Conceptual overview - what is the project intended to accomplish?
- [x] Include a broad description of the different types of users/roles and what they do.
- [x] Functional requirements (broken down by page) - what are the discrete operations the app needs to be capable of?
- [x] Third party integrations and what they do in this project - HubSpot, Stripe, Auth0, etc.
- [x] Tech Stack
  - Include frontend framework (React, Vue, Svelte, etc.)
  - Include backend framework (Express.js, etc.)
  - If you use a meta framework, where the frontend and backend are combined, then you do not need to differentiate between frontend and backend (Next, Nuxt, Sveltekit, etc.)
  - Database (PostgreSQL, MySQL, MongoDB, etc.)
  - Other important packages (UI plugins, database connectors like prisma)
  - Other tools used/needed (such as Postman)
- [x] Deployment notes (if project is currently or in the process of being deployed) - is the partner running the application on their own servers or are they using something like AWS or Azure?
- [x] Migration scripts - do we need to import any data from an existing system that the partner is using?
- [x] ***Instructions for setting up the development environment!!!*** Assume that the needed software is already installed (Node.js, Docker, etc.).
  - How do you start your project?
  - How do you initialize the database?
  - How do you set up authentication?
  - Etc.

### Optional Additional Documentation

In the repo's GitHub wiki, include the following:

- [ ] List of user workflows (each different type of user)
- [ ] Each workflow should have a corresponding wiki page, linked in the list, that either contains the workflow information or a TODO.
- [ ] Each workflow should list the pages involved
- [ ] List of user roles and what each role is able to do
- [ ] Every third party integration should have its own page describing what parts of that service are used, how, and why

These should be high level - you should not be explaining every line of code.

Closed 2024-12-13.

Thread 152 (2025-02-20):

Chassis Improvement

MahdMalik, 2025-02-20:
**Description:**
We need to redesign so that the battery holder is separated from the chassis. It must be able to be attached to the chassis using screws. It must be created using TPU elastic material.

**TODO:**
- [ ] Create chasis using C.A.D
- [ ] Separate battery holder
- [ ] create fastening holes to connect the battery to the chassis
- [ ] print battery holder with TPU elastic material

**REQUIRED SKILLS.**
- Fusion 360
- 3D printer

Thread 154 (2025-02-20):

Chassis Improvement

MahdMalik, 2025-02-20:
**Description:**
We need to redesign so that the battery holder is separated from the chassis. It must be able to be attached to the chassis using screws. It must be created using TPU elastic material.

**TODO:**
- [x] Create chasis using C.A.D
  - [x] Separate battery holder
  - [x] create fastening holes to connect the battery to the chassis
  - [x] print battery holder with TPU elastic material

**REQUIRED SKILLS.**
- Fusion 360
- 3D printer

Closed 2025-05-13.

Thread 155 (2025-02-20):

Rewire Electronics

MahdMalik, 2025-02-20:
**Description:**
We must rewire the electronics so they are cleaner to look at and alter.

**TODO:**

- [ ] Rewire all the electronics so that the soldering and wiring are cleaner and more concise.
- [ ] Crimp terminal connectors to 12 AWG wire to attach to the battery terminals.
- [ ] Use an XT90 connector to connect to the battery.
- [ ] Resolder the XT30 connectors for the output of the boost converter.
- [ ] Prepare a TP5000 board and solder magnetic terminals and LED.
- [ ] Brainstorm ways to create a board to interface the main power supply to branch into power rails for the charging stations, goals, and Raspberry Pi.
- [ ] Start brainstorming ways to design a board to house the ESP32-S2, boost converter, and power switch.

**REQUIRED SKILLS:**
- soldering
- crimping
- grip strength

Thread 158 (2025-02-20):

Sending Motor Data from Raspberry Pi to ESP32

MahdMalik, 2025-02-20:
**Description:**
Description:
Data about the motor's direction needs to be sent from the website to the motors. To do this, first we need to get what keys the user inputs (such as which arrow keys or WASD keys are pressed), and then send the keys that are pressed to the Raspberry Pi server through a socket. Then, upon receiving this direction, our Raspberry Pi then sends data through wifi to our ESP32. This ESP32 then decodes the keys that are being pressed, and then accurately sends pulses to the motor to move the robot accordingly. For now though, this issue is just about having the data being sent.

**TODO:**

- [x] Have Raspberry Pi be able to move the robot.
  - [x] Have Raspberry Pi send input data through wifi to the ESP32.
  - [x] Have ESP32 decode the data sent to get what keys the user is pressed.
- [x] Correctly send PWM signals to the pins connected to the motors, to have the motor receive movement signals. Should have code to accelerate.
  - [x] First, have pwm signals move the motor.
**REQUIRED SKILLS:**

- Esp idf
- Socket programming
- C++ (for esp32), Python (for Raspberry Pi)

Closed 2025-04-03.

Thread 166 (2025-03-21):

Begin Integration of Website with Raspberry Pi

MahdMalik, 2025-03-21:
**Description:**
As of current, we have a file set up to read from the Raspberry Pi, but it currently does nothing. We need it to actually begin calling the Raspberry Pi and getting information. Here's what needs to be done on the server end:

- [x] Establishing a connection with the raspberry pi
- [x] Having the timer be given to the raspberry pi and the updated timer given back.
- [ ] Having the scores be received from the raspberry pi on goal and being sent to the game manager
- [ ] Having the raspberry pi notify the game manager that its robots are ready
- [ ] having input from the client sent to the raspberry pi

**REQUIRED SKILLS:**
- Socket programming
-Typescript (for website), Python (for Raspberry Pi)

Closed 2025-04-13.

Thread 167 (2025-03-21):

Creating smooth motor control with Raspberry Pi Movement.

MahdMalik, 2025-03-21:
**Description:**
So we have our Raspberry Pi sent input to the ESP32 and cause it to move. Now, we need to make the controls smooth, which means using sigmoid-curves to move each of the motors to the desired power levels, based on what inputs are being pressed or if any are at all.

**TODO:**
- [ ] Decide on target PWM values for each input combination.
- [ ] Decide on equation to use for sigmoid curve, and how to effectively use that equation to smoothly accelerate and decelerate to the target PWM values.
- [ ] Integrate the equation in code, by having the PWM signals change each iteration until it reaches the target value.
- [ ] Unifying the timing such that the time it takes to reach the target value is the same in duration for any given target value, instead of relying on how fast the CPU runs.
- [ ] Integrate the code with the Raspberry Pi's current movement system, may require some changes.

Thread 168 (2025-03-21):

[BUG]

MahdMalik, 2025-03-21:
**Describe the bug**
If during confirmining of a match a user leaves, when the timer is over the bootgame server will crash because the websocket is now undefined. We need to ensure that even if the user leaves, when reading the websocket it won't crash.

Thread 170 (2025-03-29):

[BUG] Timer not updating during match.

MahdMalik, 2025-03-29:
**Describe the bug**
When a match between two bots is started, the timer never actually displays, nor are the scores for both players ever shown. This shouldn't rely on the raspberry pi, because the round does end when the timer is over, it's just that it's now displayed to the clients.
**To Reproduce**
Steps to reproduce the behavior:
1. Start a match between two players.
2. Look at the timer section, and see how it doesn't update.

**Expected behavior**
The timer should be going down every second, but it stays at "30". Internally I believe it might be counting down, but it's just not shown to the screen, which needs to be fixed.

MahdMalik, 2025-03-30:
Turns out this was only an issue when we weren't connected to th raspberry pi, because it wasn't sending back the timer; now, it works completely fine now.

Closed 2025-03-30.

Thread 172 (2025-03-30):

[BUG] Game not immedietly staring on accept/reject.

MahdMalik, 2025-03-30:
**Describe the bug**
Currently even if both players have clicked either the accept/reject button, it waits for the full timer before deciding to start the game or remove declining players from the queue. We just need to fix this so that when both players give a response, the game can immedietly start.

**To Reproduce**
Steps to reproduce the behavior:
1. Have two players in the queue.
2. Have one player either accept/reject, and have the other also accept/reject (the combination doesn't matter as long as they press it).
3. See how it still take a while for the game to start or for the players to be clicked from the queue.

**Expected behavior**
We want the game to be responsive, so once the users have put their input, the game can immedietly start.

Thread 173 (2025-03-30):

Having the Raspberry Pi check if the a ESP32 is ready.

MahdMalik, 2025-03-30:
**Description:**
Currently, the Raspberry Pi just pretend as if the ESP32's are ready when they may not actually be. We have to actually have the Raspberry Pi (specifically the GmServerPi.py program) check each of the ESP32's involved in the game and see if they're active. We can hold off on checking their battery until later.
**TODO:**
- [x] Have the GmServerPi.py call another process that actually connects with a single ESP32. It should check if the ESP is ready, and if so returns to GmServerPi.py that it's ready, otherwise false.
- [x] Have it so that if it's false, it remains false until the ESP32 is ready.

MahdMalik, 2025-04-13:
This issue should be finished now, as long as the website connects with the rasbperry pi as well. We actually get to communicate with the esp to see this.

Closed 2025-04-13.

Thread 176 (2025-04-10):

Having Raspberryi Pi Camera Streamed to Website

MahdMalik, 2025-04-10:
**Description:**
Right now, the website just shows a stream from a random Twitch channel. We need to update it so that when the camera of the Raspberry Pi is active, it is streaming to the website.

**TODO:**
- [ ] Have the camera that the Raspberry Pi is connected to at least display somewhere, to show that it works fine.
- [ ] Have the Raspberry Pi camera streamed to some website.
- [ ] Have the website embed that stream so that it is viewing the camera.

MahdMalik, 2025-05-15:
damian my goat clutched up

Closed 2025-05-15.

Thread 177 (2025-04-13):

Have esp manager file tell esp's when game is over AND automatically be ready for a new match

MahdMalik, 2025-04-13:
**Description:**
Now we have an esp manager file in the raspberry pi which asks if the esp's are ready for the match, and returns that to the website. Now, we need to check when the match ends, and send that from the game manager to the esp manager, which then alerts all the esp's that it's time to start moving. One might need to be working on this concurrently with the task of having the controller move the esp.

We also want the esp to automatically reset and be waiting for a new ready check when the game is over.

**TODO:**
- [x] have esp manager check from the game manager if the time is done at a good rate
- [x] when ready, have it send to the esp's that it can no longer be controlled, and to start waiting for another match again.

MahdMalik, 2025-04-23:
Not only does it do the assigned task fairly well, but also it becomes automatically ready for a new match, both the esp manager and the esp32 itself. Maybe there is a way to optimize it, but it works fairly well.

Closed 2025-04-23.

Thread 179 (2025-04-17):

Reinstall Raspberry Pi

IambicNine, 2025-04-17:
- Reinstall Raspberry Pi OS (latest version, no Desktop environment)
- Setup SSH server on Pi
- Properly install libcamera and PiCamera2 so that our Python scripts that utilize the camera work properly.
- Reinstall OLED display script
- Reinstall USB WIFI interface driver.
- Reinstall terminal tools (ranger, neovim, tmux, etc.)

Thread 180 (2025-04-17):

Reinstall Raspberry Pi Software

IambicNine, 2025-04-17:
**Description:**
Reinstall Raspberry Pi OS since a complication occured with packages, dependencies, especially with libcamera and PiCamera2.

**TODO:**
- Reinstall Raspberry Pi OS
- Install SSH server
- Properly install libcamera and PiCamera2 so that our Python scripts that utilize the camera work
- Reinstall USB WIFI interface driver so a hotspot can be setup
- Reinstall OLED information display service script to view IP addresses and CPU status
- Reinstall terminal software (tmux, neovim, ranger, etc.) to setup development environment.

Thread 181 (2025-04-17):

Have Motor Return To Not Moving After No Input

MahdMalik, 2025-04-17:
**Description:**
Currently when the motor is no longer receiving any input, it continues driving at the rate it was before. However this means even if user stops pressing keys, the motor will continue driving. We need to have it reset back down to being 0.

**TODO:**
- [x] Detect when the motor reaches its target (already done)
- [X] Check if the user is still inputting to drive to that amount.
- [ ] If they are no longer inputting, drive to 0, and then wait with semaphore.

So we have code that only sends input on change so this the part about detecting no input is no longer an issue. However, it seems that when there's no input the motors slow down rather than stopping completely. We need to fix that.

Closed 2025-05-01.

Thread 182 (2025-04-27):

Align PWM from ESP32 with the ESC

MahdMalik, 2025-04-27:
**Description:**
This is probably the most important task right now, if we don't do it then we won't have a working robot.

So far, the code our mentor Harold pushed at the start of the semester worked with the ESC, but now the code on the esp32_code branch doens't really work. It's not a hardware issue but rather a software issue. But now, we need the motor movement to align with the esp32_code branch's code.
**TODO:**
- [x] Figure out the reasons for what makes up the differences between harold's code and the current branch's code.
- [x] Using the new information, fix the esp32_code branch to make up for these issues.

MahdMalik, 2025-04-28:
Finally done, though now movement is kinda wonky so I shall have to fix how the movement works.

Closed 2025-04-28.

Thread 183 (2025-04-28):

[BUG] Scoreboard and Current Players In-Game not updating on game start

MahdMalik, 2025-04-28:
**Description:**
Earlier we had it so that once the game starts, the timer, score, and players in the game all have updated. However now, it seems this updating is no longer working. We have to fix it so that it starts working again.

**TODO:**
- [ ] First, figure out what made the usernames, timer, and score update in the previous code.
- [ ] Then, just map the old code to the current code so that the bug is fixed.

MahdMalik, 2025-05-15:
turns out it wasn't actually broken, so this issue is unneeded

Closed 2025-05-15.

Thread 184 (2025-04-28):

Have motors stop moving at the end of the game.

MahdMalik, 2025-04-28:
**Description:**
This is different from the other issue in that exactly when the game ends, we want to drive the motors to 0. Right now there should be code in place to do it, but it doesn't seem to work.
**TODO:**
- [ ] Find out what's going wrong with the code to stop the motors, and then just fix it.

Most likely I'll need to see what the ESP32 logs for this to work. Probably should use the cable Comet Robotics has for this.

MahdMalik, 2025-05-01:
Uh... so this issue is fixed, but now there's another problem: it seems like extra input is being sent.

Closed 2025-05-01.

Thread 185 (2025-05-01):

Have Input Only be Sent to the ESP if it's new data

MahdMalik, 2025-05-01:
**Description:**
Basically right now, the esp assumes each time something is sent, it's new data. But this isn't necessarily the case, as sometimes the data will be duplicated before being sent. We just need to quickly implement this in the rasbperry pi where if it's duplicated data from right before, we won't send it.
**TODO:**
- [ ] Store the previous iinput.
- [ ] If there's a change from that previous input, only then send it.
- [ ] Make the new input the previous input after each iteration.

MahdMalik, 2025-05-01:
Done. Now just a few more bugs to work out, and we're finally golden.

Closed 2025-05-01.

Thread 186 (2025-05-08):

Update Code and READMe Files for Next Semester's Members

MahdMalik, 2025-05-08:
**Description:**
Now that we're pretty much at the end of the next semester, we need to prepare so that the team that's taking over after us will be able to get started without being lost on where to begin or how certain things work. This task should focus on the code side first.

**TODO:**
- [x] Update main website's README file to reflect new changes made and how to boot up the server and change ip addresses in the env file.
- [x] Update ESP32 branch's README to give a brief overview of how movement works, and how to connect with the Raspberry Pi.
- [x] Update Raspberry Pi branch's README to give a brief overview of what files are needed, how to access the raspbberry pi, and how to connect it with the esp and website.
- [x] Briefly review all code changes this semester, and see if any additional comments need to be added to make certain topics clearer.

MahdMalik, 2025-05-15:
Took a really long time but finished commenting everything that needed commenting as well as sorting out the README's to be more clear in what they say.

Closed 2025-05-15.

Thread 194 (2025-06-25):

Redesign Goal Launching Mechanism

hhllba, 2025-06-25:
- Research ways to launch a ball
- Research how far ball needs to be launches (minimum)
- Draw and CAD prototypes
-

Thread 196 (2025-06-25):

Research A Recharging Station

hhllba, 2025-06-25:

hhllba, 2025-07-21:
Update:

We are no longer fully  implementing this issue this semester. However, we are adding a recharging mechanism within the chassis.

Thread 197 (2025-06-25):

Chassis Redesign

hhllba, 2025-06-25:
Given changes:

New Lithium-Ion Battery
ESP32
Motor controller
Switch
New Wheels

Redesign a new chassis that encloses components.

- Speak to David about changes
- Scale the current chassis down a half
- removing the enclosement for current battery

hhllba, 2025-07-21:
Update: 21/07/25

Developing new chassis design, will be done at the end of the week. I will print next Monday.

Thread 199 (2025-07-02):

Landing page:

TortCode, 2025-07-02:
- [x] Ask if the user is a player or guest
- [x] Redirect promptly
- [x] Guest page (/guest)
- [x] Twitch stream

khaledalshiddi, 2025-07-13:
all are done as of today.

Closed 2025-07-13.

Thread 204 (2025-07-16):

[Feature]  Create Script to Run Raspberry Pi Programs

AmmarMohammed01, 2025-07-16:
**Feature Description**
Currently, we have to navigate to Soccer-Robots/scripts directory and run EspManager.py, GmServerPi.py, and ControllerPi.py by typing out the python execution command individually.
We want to make a script that can launch all of these programs by just running one file.

**Requirements**
- [x] Create a shell file or any viable scripting method to run the three python programs that run on the Raspberry Pi.
- [x] Document the process to run the script file in the README.md

khaledalshiddi, 2025-07-23:
Updated readme

Closed 2025-07-23.

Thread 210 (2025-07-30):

Writing Code for Goal Post

AmmarMohammed01, 2025-07-30:
Need to write code for Goal Post.
The goal post should increment the scoreboard whenever a player scores a goal.

- Write Nuxt APIs to interact with the current scoreboard and increment the counter.
- Write code on the ESP microcontroller to call the Nuxt APIs to increment the respective player score.
- Need to make sure ESP doesn't count duplicate goal scores.
- Write code to control ball-return mechanism.

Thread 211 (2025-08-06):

End of Semester Requirements

AmmarMohammed01, 2025-08-06:
# End of Semester Requirements

The following checklists are what is required for your code to be considered acceptable at the end of the semester. The general purpose is to ensure that someone can run your code without encountering any errors and everything the next team needs will be easy to find. ***If your project cannot be run based on the information and files on GitHub, your final project grade will be greatly reduced and/or your team will receive an incomplete until the information needed to run your project is provided!***

One potential way to make it easy to track all of these tasks is to create issues for each of the required tasks ([see this page about GitHub issues](https://docs.github.com/en/issues/tracking-your-work-with-issues/quickstart#adding-a-task-list)). The first item in the [Project Structure/Files](#project-structurefiles) section would look something like this to automatically check the box when issue 3 is closed:

```markdown
- [ ] #3 Database Files
```

## Project Structure/Files

These requirements must be met (in the main branch of your project) by the time your final report is due.

- [ ] The most up to date version of all frontend and backend code
- [ ] Database Files
  - [ ] If using docker: `docker-compose.yml` at top level for project database.
  - [ ] Database Schema
    - If using Prisma: `schema.prisma` in a top level `prisma` folder
    - If using other database: A file with a descriptive name used to create your database schema (e.g. `schema.sql`)
- [ ] `.env.example` file containing NON-SENSITIVE environment variables (Auth0 Issuer, dev database url, etc). Sensitive environment variables should be replaced with example data such as `CLIENT_SECRET='EXAMPLE_CLIENT_SECRET'` so that future groups know that the environment variable is required.
- [ ] Figma design files in a top level folder named `figma`.
- [ ] Any migration scripts, dev scripts, etc. (if any exist) belong in a top level `scripts` folder. If the project has separate frontend/backend folders, the `scripts` folder should be in the backend folder.
- [ ] Any other important files should be included in an appropriately named folder (such as `docs`, `documentation`, `notes`, etc.).

## Documentation

A README.md file at the top level containing the following:

- [ ] Conceptual overview - what is the project intended to accomplish?
  - Include a broad description of the different types of users/roles and what they do.
- [ ] Functional requirements (broken down by page) - what are the discrete operations the app needs to be capable of?
- [ ] Third party integrations and what they do in this project - HubSpot, Stripe, Auth0, etc.
- [ ] Tech Stack
  - Include frontend framework (React, Vue, Svelte, etc.)
  - Include backend framework (Express.js, etc.)
  - If you use a meta framework, where the frontend and backend are combined, then you do not need to differentiate between frontend and backend (Next, Nuxt, Sveltekit, etc.)
  - Database (PostgreSQL, MySQL, MongoDB, etc.)
  - Other important packages (UI plugins, database connectors like prisma)
  - Other tools used/needed (such as Postman)
- [ ] Deployment notes (if project is currently or in the process of being deployed) - is the partner running the application on their own servers or are they using something like AWS or Azure?
- [ ] Migration scripts - do we need to import any data from an existing system that the partner is using?
- [ ] ***Instructions for setting up the development environment!!!*** Assume that the needed software is already installed (Node.js, Docker, etc.).
  - How do you start your project?
  - How do you initialize the database?
  - How do you set up authentication?
  - Etc.

### Additional Documentation

In the repo's GitHub wiki, include the following:

- [ ] List of user workflows (each different type of user)
- [ ] Each workflow should have a corresponding wiki page, linked in the list, that either contains the workflow information or a TODO.
- [ ] Each workflow should list the pages involved
- [ ] List of user roles and what each role is able to do
- [ ] Every third party integration should have its own page describing what parts of that service are used, how, and why

These should be high level - you should not be explaining every line of code.

## Examples
See [Comet Cupboard](https://github.com/UTDallasEPICS/Comet-Cupboard/wiki#shopping-functionality) and [Wellness Center](https://github.com/UTDallasEPICS/Wellness-Center-Older-Adults/wiki) for examples of what documentation can look like.

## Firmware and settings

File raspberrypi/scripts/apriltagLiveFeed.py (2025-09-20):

import io
import logging
import socket
import socketserver
from http import server
from threading import Condition
import cv2
import numpy as np
from pupil_apriltags import Detector
import picamera2
from picamera2.encoders import JpegEncoder
from picamera2.outputs import FileOutput
from libcamera import Transform
import RPi.GPIO as GPIO
import pigpio
import threading
import multiprocessing
from multiprocessing import Process, Queue

# Set up the servo motor control
servo_pin = 18
pwm = pigpio.pi()
pwm.set_mode(servo_pin, pigpio.OUTPUT)
pwm.set_PWM_frequency(servo_pin, 50)

# Initial pulse width
pw = 1450
pwm.set_servo_pulsewidth(servo_pin, pw)

# HTML page with JS to detect arrow key presses and send POST requests
PAGE = """\
<html>
<head>
<title>Picamera2 MJPEG Streaming with AprilTag Detection</title>
<script type="text/javascript">
    document.addEventListener('keydown', function(event) {
        var key;
        if (event.key === 'ArrowUp') {
            key = 'up';
        } else if (event.key === 'ArrowDown') {
            key = 'down';
        } else if (event.key === 'ArrowLeft') {
            key = 'left';
        } else if (event.key === 'ArrowRight') {
            key = 'right';
        }

        if (key) {
            var xhr = new XMLHttpRequest();
            xhr.open("POST", "/control", true);
            xhr.setRequestHeader("Content-Type", "application/x-www-form-urlencoded");
            xhr.send("key=" + key);
        }
    });
</script>
</head>
<body>
<h1>Picamera2 MJPEG Streaming with AprilTag Detection</h1>
<img src="stream.mjpg" width="640" height="480" />
<p>Use the arrow keys to control the camera.</p>
</body>
</html>
"""

# Buffer for streaming the camera frames
class StreamingOutput:
    def __init__(self):
        self.frame = None
        self.condition = Condition()
        
    def set_frame(self, frame):
        with self.condition:
            self.frame = frame
            self.condition.notify_all()

# HTTP request handler
class StreamingHandler(server.BaseHTTPRequestHandler):
    def do_GET(self):
        if self.path == '/':
            self.send_response(301)
            self.send_header('Location', '/index.html')
            self.end_headers()
        elif self.path == '/index.html':
            content = PAGE.encode('utf-8')
            self.send_response(200)
            self.send_header('Content-Type', 'text/html')
            self.send_header('Content-Length', len(content))
            self.end_headers()
            self.wfile.write(content)
        elif self.path == '/stream.mjpg':
            self.send_response(200)
            self.send_header('Age', 0)
            self.send_header('Cache-Control', 'no-cache, private')
            self.send_header('Pragma', 'no-cache')
            self.send_header('Content-Type', 'multipart/x-mixed-replace; boundary=FRAME')
            self.end_headers()
            try:
                while True:
                    with output.condition:
                        output.condition.wait()
                        frame = output.frame
                    self.wfile.write(b'--FRAME\r\n')
                    self.send_header('Content-Type', 'image/jpeg')
                    self.send_header('Content-Length', len(frame))
                    self.end_headers()
                    self.wfile.write(frame)
                    self.wfile.write(b'\r\n')
            except Exception as e:
                logging.warning(
                    'Removed streaming client %s: %s',
                    self.client_address, str(e))
        else:
            self.send_error(404)
            self.end_headers()
            
    def do_POST(self):
        global pw
        if self.path == '/control':
            content_length = int(self.headers['Content-Length'])
            post_data = self.rfile.read(content_length).decode('utf-8')
            key = post_data.split('=')[1]
            moveSize = 10

            # Adjust the pulse width (pw) based on key press
            if key == 'left':
                if pw < 1525:  # Move right within bounds
                    pw += moveSize
            elif key == 'right':
                if pw > 1380:  # Move left within bounds
                    pw -= moveSize
            
            # Set the pulse width to control the servo
            pwm.set_servo_pulsewidth(servo_pin, pw)
            print(f"Key pressed: {key}, Pulsewidth: {pw}")

            self.send_response(200)
            self.end_headers()

# HTTP server setup
class StreamingServer(socketserver.ThreadingMixIn, server.HTTPServer):
    allow_reuse_address = True
    daemon_threads = True

# Function to get the Raspberry Pi's IP address
def get_ip_address():
    s = socket.socket(socket.AF_INET, socket.SOCK_DGRAM)
    try:
        # Doesn't even have to be reachable
        s.connect(("8.8.8.8", 80))
        ip = s.getsockname()[0]
    except Exception:
        ip = "localhost"
    finally:
        s.close()
    return ip

def apriltag_process(frame_queue, result_queue, camera_params, tag_size):
    # Initialize the AprilTag detector
    at_detector = Detector(
        families="tag36h11",
        nthreads=4,  # Use all 4 cores
        quad_decimate=2.0,  # Increase for faster processing
        quad_sigma=0.0,
        refine_edges=1,
        decode_sharpening=0.25,
        debug=0
    )
    while True:
        frame = frame_queue.get()
        if frame is None:
            break
        # Convert the frame to grayscale
        img_gray = cv2.cvtColor(frame, cv2.COLOR_BGR2GRAY)
        # Detect the AprilTags in the frame
        tags = at_detector.detect(img_gray, estimate_tag_pose=True, camera_params=camera_params, tag_size=tag_size)
        result_queue.put((frame, tags))

def main():
    global output, pwm, pw

    output = StreamingOutput()

    # Define camera parameters for pose estimation
    fx = 300  # Adjusted focal length
    fy = 300
    cx = 160  # Adjusted principal point
    cy = 120
    camera_params = [fx, fy, cx, cy]
    tag_size = 0.16  # Size of the AprilTag in meters (adjust to your tag size)

    # Queues for inter-process communication
    frame_queue = Queue(maxsize=2)
    result_queue = Queue(maxsize=2)

    # Start the AprilTag detection process
    process = Process(target=apriltag_process, args=(frame_queue, result_queue, camera_params, tag_size))
    process.start()

    # Camera setup with reduced resolution
    picam2 = picamera2.Picamera2()
    config = picam2.create_video_configuration(
        main={"size": (320, 240), "format": "RGB888"},
        transform=Transform(vflip=True, hflip=True)
    )
    picam2.configure(config)

    # Start the camera
    picam2.start()

    # Start a thread to handle frame capture and processing
    def capture_frames():
        while True:
            frame = picam2.capture_array()
            if not frame_queue.full():
                frame_queue.put(frame)
            # Check for results and overlay detections
            if not result_queue.empty():
                processed_frame, tags = result_queue.get()
                # Draw detections on the frame
                for tag in tags:
                    corners = tag.corners.astype(int)
                    cv2.polylines(processed_frame, [corners], True, (0, 255, 0), thickness=2)
                    cX = int((corners[0, 0] + corners[2, 0]) / 2)
                    cY = int((corners[0, 1] + corners[2, 1]) / 2)
                    # Calculate the rotation of the tag
                    dx = corners[2, 0] - corners[0, 0]
                    dy = corners[2, 1] - corners[0, 1]
                    rotation = np.degrees(np.arctan2(dy, dx))
                    rotation = (rotation + 45) % 360  # Adjust the rotation by adding 45 degrees

                    # Put the center coordinates near the tag center
                    center_text = "x={:d}, y={:d}".format(cX, cY)
                    cv2.putText(processed_frame, center_text, (cX, cY + 20), cv2.FONT_HERSHEY_SIMPLEX, 0.5, (0, 255, 0), 2)

                    # Display the tag id
                    id_text = "id={:d}".format(tag.tag_id)
                    cv2.putText(processed_frame, id_text, (cX, cY - 20), cv2.FONT_HERSHEY_SIMPLEX, 0.5, (0, 255, 0), 2)

                    # Display the rotation
                    rotation_text = "rotation={:.2f} deg".format(rotation)
                    cv2.putText(processed_frame, rotation_text, (cX, cY - 40), cv2.FONT_HERSHEY_SIMPLEX, 0.5, (0, 255, 0), 2)

                    # Get the pose estimation (translation vector)
                    if tag.pose_t is not None:
                        t = tag.pose_t  # Translation vector
                        z = t[2][0]  # Distance along Z-axis (forward from camera)
                        z_text = "z={:.2f} m".format(z)
                        cv2.putText(processed_frame, z_text, (cX, cY + 40), cv2.FONT_HERSHEY_SIMPLEX, 0.5, (0, 255, 0), 2)

                # Encode the frame as JPEG
                ret, jpeg = cv2.imencode('.jpg', processed_frame)
                if ret:
                    output.set_frame(jpeg.tobytes())
            else:
                # If no new detection results, use the original frame
                ret, jpeg = cv2.imencode('.jpg', frame)
                if ret:
                    output.set_frame(jpeg.tobytes())

    threading.Thread(target=capture_frames, daemon=True).start()

    try:
        address = ('', 8000)
        ip = get_ip_address()
        print(f"\n\n\nStarting server at http://{ip}:8000\n\n\n")
        server = StreamingServer(address, StreamingHandler)
        server.serve_forever()
    finally:
        picam2.stop()
        process.terminate()
        process.join()
        pwm.set_PWM_dutycycle(servo_pin, 0)
        pwm.set_PWM_frequency(servo_pin, 0)

if __name__ == '__main__':
    main()

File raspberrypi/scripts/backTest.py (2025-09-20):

# Import necessary modules
import io
import logging
import socket
import socketserver
from http import server
from threading import Condition
import threading
import multiprocessing
from multiprocessing import Process, Queue
import cv2
import numpy as np
from pupil_apriltags import Detector
import picamera2
from picamera2.encoders import JpegEncoder
from picamera2.outputs import FileOutput
from libcamera import Transform
import time

# HTML page with movement commands reference and charging status message
PAGE = """\
<html>
<head>
<title>Picamera2 MJPEG Streaming with AprilTag Detection</title>
<script type="text/javascript">
    document.addEventListener('DOMContentLoaded', function() {
        var eventSource = new EventSource('/events');
        eventSource.onmessage = function(e) {
            document.getElementById('status_message').textContent = e.data;
        };
    });
</script>
<style>
    body { font-family: Arial, sans-serif; }
    #commands { margin-top: 20px; }
</style>
</head>
<body>
<h1>Picamera2 MJPEG Streaming with AprilTag Detection</h1>
<img src="stream.mjpg" width="640" height="480" />
<p id="status_message">Loading...</p>
<div id="commands">
    <h3>Movement Commands Reference:</h3>
    <ul>
        <li>1: Move Forward</li>
        <li>2: Move Backward</li>
        <li>3: Rotate Left</li>
        <li>4: Rotate Right</li>
        <li>0: Stop</li>
    </ul>
</div>
</body>
</html>
"""

# Buffer for streaming the camera frames
class StreamingOutput:
    def __init__(self):
        self.frame = None
        self.condition = Condition()
        self.clients = []

    def set_frame(self, frame):
        with self.condition:
            self.frame = frame
            self.condition.notify_all()

# HTTP request handler
class StreamingHandler(server.BaseHTTPRequestHandler):
    def do_GET(self):
        if self.path == '/':
            self.send_response(301)
            self.send_header('Location', '/index.html')
            self.end_headers()
        elif self.path == '/index.html':
            content = PAGE.encode('utf-8')
            self.send_response(200)
            self.send_header('Content-Type', 'text/html')
            self.send_header('Content-Length', len(content))
            self.end_headers()
            self.wfile.write(content)
        elif self.path == '/stream.mjpg':
            self.send_response(200)
            self.send_header('Age', 0)
            self.send_header('Cache-Control', 'no-cache, private')
            self.send_header('Pragma', 'no-cache')
            self.send_header('Content-Type', 'multipart/x-mixed-replace; boundary=FRAME')
            self.end_headers()
            try:
                while True:
                    with output.condition:
                        output.condition.wait()
                        frame = output.frame
                    self.wfile.write(b'--FRAME\r\n')
                    self.send_header('Content-Type', 'image/jpeg')
                    self.send_header('Content-Length', len(frame))
                    self.end_headers()
                    self.wfile.write(frame)
                    self.wfile.write(b'\r\n')
            except Exception as e:
                logging.warning(
                    'Removed streaming client %s: %s',
                    self.client_address, str(e))
        elif self.path == '/events':
            # SSE endpoint for sending status messages
            self.send_response(200)
            self.send_header('Content-Type', 'text/event-stream')
            self.send_header('Cache-Control', 'no-cache')
            self.end_headers()
            try:
                while True:
                    message = status_message
                    self.wfile.write(f"data: {message}\n\n".encode('utf-8'))
                    time.sleep(1)
            except Exception as e:
                pass
        else:
            self.send_error(404)
            self.end_headers()

# HTTP server setup
class StreamingServer(socketserver.ThreadingMixIn, server.HTTPServer):
    allow_reuse_address = True
    daemon_threads = True

# Function to compute movement instruction based on the current state
def compute_movement(car_state, cX, cY, rotation, targetX, targetY, desired_rotation):
    # Compute vector to target
    deltaX = targetX - cX
    deltaY = targetY - cY

    # Desired angle to target
    desired_angle = (np.degrees(np.arctan2(deltaY, deltaX)) + 360) % 360

    # Corrected angle difference calculation
    angle_diff = ((rotation - desired_angle + 180) % 360) - 180

    # Distance to target
    distance = np.hypot(deltaX, deltaY)

    # Thresholds
    angle_threshold = 15  # Increased to prevent oscillations
    distance_threshold = 20  # Adjusted based on testing
    rotation_threshold = 15  # Increased for final orientation

    # Movement commands
    # 1: Move Forward
    # 2: Move Backward
    # 3: Rotate Left
    # 4: Rotate Right
    # 0: Stop

    if car_state['state'] == 0:
        # Rotate to face the target
        if angle_diff < -angle_threshold:
            movement = 3  # Rotate Left
        elif angle_diff > angle_threshold:
            movement = 4  # Rotate Right
        else:
            movement = 0
            car_state['state'] = 1
    elif car_state['state'] == 1:
        # Move towards the target
        if distance > distance_threshold:
            movement = 1
        else:
            movement = 0
            car_state['state'] = 2
    elif car_state['state'] == 2:
        # Rotate to desired final orientation
        rotation_diff = ((rotation - desired_rotation + 180) % 360) - 180
        if rotation_diff < -rotation_threshold:
            movement = 3  # Rotate Left
        elif rotation_diff > rotation_threshold:
            movement = 4  # Rotate Right
        else:
            movement = 0
            car_state['state'] = 3
    else:
        # Arrived and correctly oriented
        movement = 0

    # Logging for debugging
    print(f"State: {car_state['state']}, Movement: {movement}, Desired Angle: {desired_angle:.2f}, Rotation: {rotation:.2f}, Angle Diff: {angle_diff:.2f}")

    return movement

# Process to handle AprilTag detection
def apriltag_process(frame_queue, result_queue, camera_params, tag_size):
    # Initialize the AprilTag detector
    at_detector = Detector(
        families="tag36h11",
        nthreads=4,  # Use all 4 cores
        quad_decimate=2.0,  # Adjust for performance
        quad_sigma=0.0,
        refine_edges=1,
        decode_sharpening=0.25,
        debug=0
    )
    while True:
        frame = frame_queue.get()
        if frame is None:
            break
        # Convert the frame to grayscale
        img_gray = cv2.cvtColor(frame, cv2.COLOR_BGR2GRAY)
        # Detect the AprilTags in the frame with pose estimation
        tags = at_detector.detect(img_gray, estimate_tag_pose=True, camera_params=camera_params, tag_size=tag_size)
        result_queue.put((frame, tags))
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

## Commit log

2025-02-27 changed button circle and added comments
2025-03-29 added connection to actual raspberry pi
2025-03-30 now works with the raspberry pi
2025-04-27 fixed on more bug. Issue is, scoreboard doesn't seem to be showing the current game now, that needs to be fixed
2025-05-01 fixed some bugs, still might have an issue when sending the timer duration to the pi though
2025-06-25 Made Join Queue button line up with Queue box. Also, Lined up Queue, Leaderboard, and Up Next sections
2025-07-13 Made a landing page with guest page. In the guest page, embedded twitch and showed matches as well as chnaged the nav bar to have a more minimal look.
2025-09-11 create cad folder and upload existing cad files
    [BUMPERFINAL.SLDPRT, CHASSIS.SLDPRT, ESP32 Robot Wheel v7.f3d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]
2025-09-18 Designed new goalpost designs for bigger robot
    [goalpost.SLDPRT, goalpost_alt.SLDPRT]
2025-09-18 Add esp32 folder
2025-09-20 Fix GitHub Workflow (#223)
    * try removing the brackets
    * Use node v20 in gh action
    * Generate prisma client allowing no models
    * Disable ERD when generating prisma client
2025-09-25 designed new launcher assembly
    [launcher_assembly.SLDASM, launcher_wheel.SLDPRT, motor.SLDASM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]
